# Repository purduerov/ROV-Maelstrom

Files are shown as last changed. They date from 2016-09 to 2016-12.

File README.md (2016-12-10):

# ROV-Maelstrom

Purdue IEEE designed an ROV (Remotely Operated underwater Vehicle) to compete in the 2016 [MATE international competition](http://www.marinetech.org/rov-competition-2/). ROV *Maelstrom* was the cumulation of this effort that resulted in a 13th place finish. For more information visit [purdueieee.org/rov](http://purdueieee.org/rov).

Our design is hearby open-sourced in order to share what we have done with other MATE teams and those who are interested. While not all of our designs worked as planned, we share these files in order to assist thoughs who may need it and inspire others with these ideas.

Maelstrom

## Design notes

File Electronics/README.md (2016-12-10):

# ROV-Maelstrom-Electronics

ROV Maelstrom’s electronics were designed to facilitate easy and reliable command over the course of the ROV’s lifetime. Command starts at the Control Center, the surface electronics that the user interfaces with. This includes a laptop computer, a network router, and a 48 V power supply protected with a 40-A fuse. 

Communication with the Control Center is done through the tether with a Category 5 Ethernet cable, which provides high bandwidth and noise immunity. The power is transmitted through two 12-AWG marine wires. Onboard the ROV, it steps down the 48 V to 12 V, 5 V, and 3.3 V for use by the ROV’s eight T200 thrusters, the hydraulics motor, and the Main Electronics inside the Electronics Tube. The Power Distribution Box contains the Power Distribution Board, which handles the 48 V to 12 V power conversion and thruster control. Inside of the Electronics Tube are the Main Microcontroller Board, the Power Regulator Board, and the Application Board which are all connected via the Backplane. The Main Microcontroller Board handles the central logic processing of the ROV and communication with the surface, Application Board, and Power Distribution Board. The Power Regulator Board supplies the 5 V required by the electronics inside of the Electronics Tube, while the Application Board controls the LED lighting of ROV Maelstrom. The Navigation Board is used for pressure and attitude measurements and is placed outside of the Electronics Tube for reduced magnetic interference and direct contact with water. The board also hosts the sonar transmitter used for GPS-like navigation. The Sonar Receiver Board in the Control Center is used to receive and filter the sonar transmission signals. The printed circuit boards were designed in-house with the use of CadSoft's EAGLE software and then hand populated

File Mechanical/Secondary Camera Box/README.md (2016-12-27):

# Secondary Camera Boxes

These are the boxes for the secondary cameras. They are not able to rotate like the primary camera tube.

The cameras themselves had a  1-2 second delay since they were cheaper than the main camera and webcams couldn't easily be used with the STM32F4 microcontroller.

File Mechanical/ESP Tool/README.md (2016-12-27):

# ESP Tool

The Environmental Sample Processor(ESP) tool was designed to pick up the ESP cable connector and attach it to the power and communications hub in the water. The part was not fully manufactured or tested.

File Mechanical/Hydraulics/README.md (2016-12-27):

# Hydraulics

The hydraulic system had an open loop design, and pulled in pool water, pressurized it, and sent it to a solenoid. The water was distributed by the solenoid and used to actuate the main claw, ESP tool, Wellhead tool, and other manipulators. After being used, it returned to the pool water. We used an M100 waterproof motor to power the pump. The solenoid was in an open faced housing, and filled with Magic Gel, a potting substance that sets to the consistency of gelatin. The Magic Gel insulated and water proofed the solenoid. While effective, it is permanent and needs to be removed before working on it and reapplied. We used a hydraulic system instead of electric motors for direct actuation to make waterproofing the system easier. Due to electrical issues the full system was never operated on the vehicle.

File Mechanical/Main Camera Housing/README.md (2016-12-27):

# Main Camera Housing 

The Camera housing is made from a polycarbonate tube and two aluminum endcaps. The camera is mounted onto a servo in the middle of the tube, and the servo is attached by a dowel to the endcap. This allows the camera to spin and gives the pilot a 180 degree field a view. The endcaps are sealed with two x-profile o-rings. 

For the cameras themselves we used IP addressable cameras for ROV Maelstrom. The signals from these cameras were then passed to an Ethernet switch. This switch then handled figuring out what information needed to be sent to the surface.

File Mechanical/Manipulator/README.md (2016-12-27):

# Manipulator

The manipulator is driven from a hydraulic piston attached to a base. There are three fingers attached to the base, with two on the top and one on the bottom. The design is optimized to pick up pipes, the most common prop in the competition.  The tips on the claw are 3D printed, allowing for several designs to be made, and quick changes between the two tips.

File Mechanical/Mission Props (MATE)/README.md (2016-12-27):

# Mission Props

These are the props provided to the team by the MATE competition.

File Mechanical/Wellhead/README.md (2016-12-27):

# Wellhead

The wellhead tool has four grooves in it to position bolts so that they can be installed in one attempt. It requires that a person positions the bolts in the tool by hand. The tool will then clamp down on them. The ROV then moves over the wellhead and aligns the bolts. When the tool releases the bolts, then all drop into place in their correct positions.

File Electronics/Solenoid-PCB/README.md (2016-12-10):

# Solenoid-PCB
This board contains a shift register to control solenoids on the ROV.

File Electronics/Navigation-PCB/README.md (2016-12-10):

# ROV-Maelstrom-Navboard

This board contains the IMU to assist with ROV positioning. Additionally it containspiezo driver to send pulses to the sonar receiver board. The full sonar system was never fullly implemented this season.

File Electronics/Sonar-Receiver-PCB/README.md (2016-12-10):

# PCB-Maelstrom-Sonar-Receiver

The sonar receiver board is placed at the surface of the pool. It receives the piezo pulses from the ROV and uses the information to pinpoint the ROV's position underwater. The full sonar system was never fullly implemented this season.

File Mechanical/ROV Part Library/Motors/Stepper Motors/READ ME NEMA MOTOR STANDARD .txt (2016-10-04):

NEMA Motor Standard

There is no NEMA motor naming convention due to the fact that all NEMA Motor Sizes 
are controlled with Configurations.  Therefore there is absolutely no need to add 
any new files to this folder.

If you need a NEMA Stepper Motor Size and you do not know what a configuration is or 
how to use them, please contact the Mechanical Team Lead 
(Joshua Berg -> berg30@purdue.edu)

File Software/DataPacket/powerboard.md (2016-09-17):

# PowerBoard CAN Communication

Main Micro -> PowerBoard Micro (Packet 1)
-----------------------------------------
Byte # |   Description   | Type
-------|-----------------|------
  00   |   Packet Type   |  0x48 - 'H'
  01   |        T1       |	Signed int (1 byte)
  02   |        T2       |  Signed int (1 byte)
  03   |        T3       |	Signed int (1 byte)
  04   |        T4       |  Signed int (1 byte)
  05   |       Empty     |	Empty
  06   |       Empty     |  Empty
  07   |     Pump ESC    |  1 byte (0 to 255 PWM Val)
  
Main Micro -> PowerBoard Micro (Packet 2)
-----------------------------------------
Byte # |   Description   | Type
-------|-----------------|------
  00   |   Packet Type   |  0x56 - 'V'
  01   |        T5       |	Signed int (1 byte)
  02   |        T6       |  Signed int (1 byte)
  03   |        T7       |	Signed int (1 byte)
  04   |        T8       |  Signed int (1 byte)
  05   |       Empty     |	Empty
  06   |       Empty     |  Empty
  07   |       Empty     |  1 byte - bool for pid / manual control

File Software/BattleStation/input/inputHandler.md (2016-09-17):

initInputHandler()
	init SDL library
	while the program is running
		check if there's a new joystick
		if so
			update queue of joysticks
			assign button-to-function mapping
			show it on GUI
		check if there's a missing joystick
		if so
			update queue
			show it on GUI
		check if button from any joysticks were pressed
		if so
			call function

a vector of SDL_Joystick* will be used to hold joysticks

Questions
1. How do I know that a joystick is unplugged?
2. If someone unplugs and replugs really quickly, will it slow the button input from my program? And if so, how much?
3. If someone unpluags and replugs a new joystick, in between the two checks, how do I know if they are different joysticks? (will they have the same ID?)
4. how do I show it on GUI?
5.

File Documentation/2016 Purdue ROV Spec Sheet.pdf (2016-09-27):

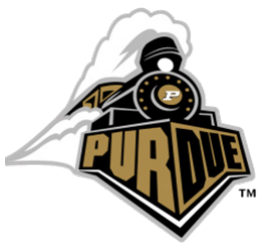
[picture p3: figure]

# PROVEN ROBOTICS

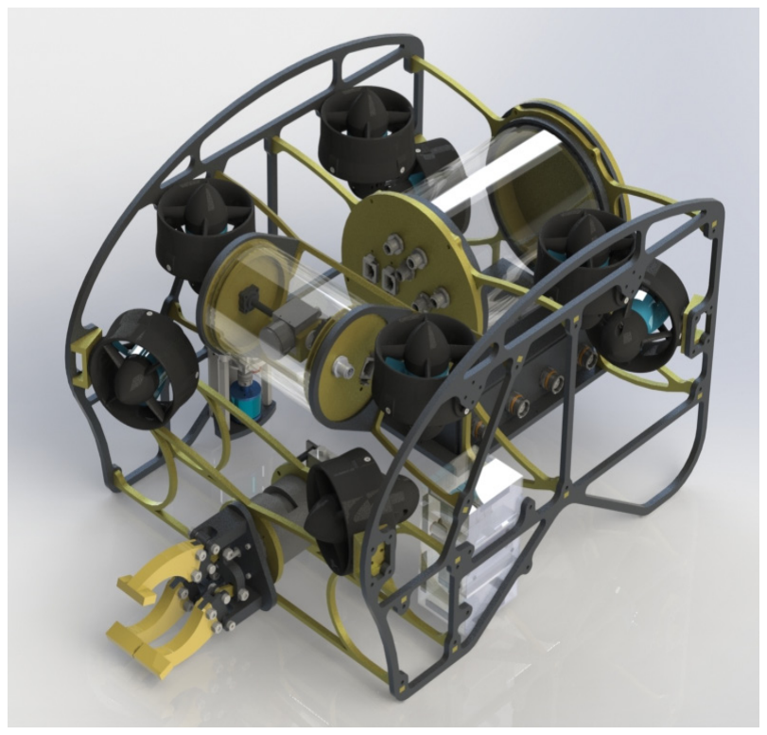
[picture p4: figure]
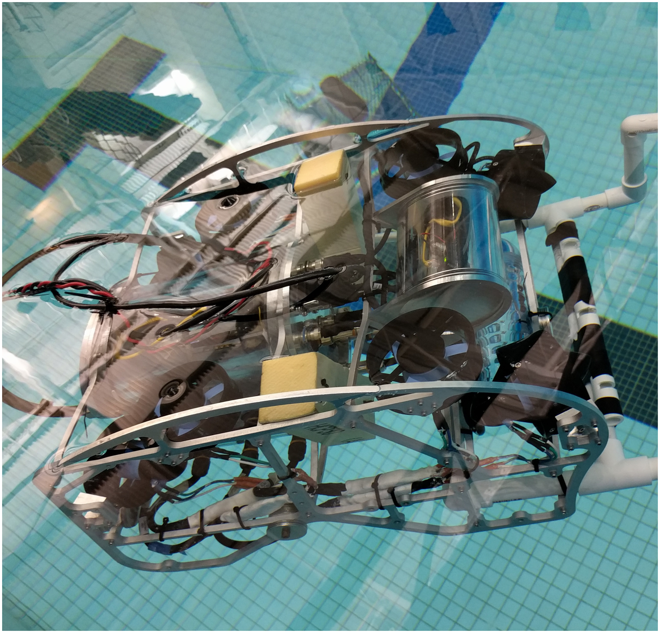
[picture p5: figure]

# ROV MAELSTROM

### West Lafayette, Indiana, USA

Total Mass in Air:
12.8 kg

Overall Dimensions:
48.3 cm x 39.4 cm x 33.0 cm

Primary Material:
Aluminum 6061 T-6
Stainless Steel
Polycarbonate

Total Cost of ROV:
$10,500

Total ROV Design Man-Hours: 6,500 hours

Safety Features:
Enclosed Pump
Fused Main Power
Shrouded Propellers
Software Disconnection Timeouts Hydraulics Pressure Release Valve Epoxy and Heat Shrink Sealed Wires

Special Features:
Onboard Open-Loop Hydraulics LED-Illuminated Camera with Tilt Custom Built On-Board Electronic System Four-Axis Sonar Based Positioning System

Carolyn Leweling

Electrical Engineering
Sophomore: Lead Sponsorship Coordinator
Electrical Team
2nd Year Competing

Dan Schillizzi

Mechanical Engineering
Sophomore: Mechanical Team 2nd Year Competing

Joseph Pejril

Mechanical Engineering
Junior: Mechanical Team
ROV Pilot
2nd Year Competing

Kyle Rakos

Computer Engineering
Junior: CEO
2nd Year Competing

Luke McBee

Computer Engineering
Sophomore: Electrical
Team Lead
2nd Year Competing

Matt Molo

Computer Science
Junior: Software Team Lead ROV Pilot
3rd Year Competing

Rodolfo E. Leiva

Electrical Engineering
Junior: Electrical Team
2nd Year Competing

Ryan McBee

Computer Engineering
Sophomore: Embedded
Software Subteam Lead
2nd Year Competing

Samuel Deghuee

Electrical Engineering
Sophomore: Electrical Team 2nd Year Competing

Sanay Shah

Industrial Engineering
Sophomore: COO
2nd Year Competing

Teal Dowd

Mechanical Engineering
Sophomore: Mechanical Team 2nd Year Competing

Joshua Berg

Mechanical Engineering
Junior: Mechanical Team Lead 2nd Year Competing

Charlie Su

Computer Science/Physics
Sophomore: Software Team
2nd Year Competing

Alex Ruffino

Mechanical Engineering
Freshman: Sponsorship
Coordinator
Mechanical Team
1st Year Competing

Rohit Srivastava

Biomedical Engineering
Freshman: Mechanical Team
1st Year Competing

Ajay Gopakumar

Computer Engineering
Freshman: Software Team
1st Year Competing

Nicholas Loffredo

Electrical Engineering
Sophomore: Electrical Team 1st Year Competing

Henry Shi

Industrial Engineering
Sophomore: Technical Writer 1st Year Competing

Yuqin (Sophia) Duan

Computer Engineering
Freshman: Software &
Mechanical Team
1st Year Competing

Jared Borg

Mechanical Engineering
Freshman: Mechanical Team
5th Year Competing

Scott Giammatteo

Aerospace Engineering
Freshman: Mechanical Team
1st Year Competing

Mimansa Verma

Computer Engineering
Freshman: Software Team
1st Year Competing

Jakob Andrén

Engineering Physics
Senior: Electrical &
Software Team
1st Year Competing

Michael Reeves

Physics/Computer Science
Freshman: Software Team
1st Year Competing

Nathan Glotzbach

Physics
Freshman: Software Team
1st Year Competing

Ben Maxfield

Computer Science
Freshman: Software Team
1st Year Competing

Oksana Makarova

Electrical Engineering/Physics Freshman: Software Team
1st Year Competing

Katie Lothrop

Mechanical Engineering
Sophomore: Mechanical Team 1st Year Competing

Amandeep Singh

Mechanical Engineering
Sophomore: Software Team
1st Year Competing

McKenzie White

Environmental and Ecological Engineering
Freshman: Mechanical Team
1st Year Competing

Joel Copi

Computer Engineering
Freshman: Software Team
1st Year Competing

Bayley Clausen

Mechanical Engineering
Junior: Electrical Team
2nd Year Competing

Jason King

Computer Engineering
Freshman: Software Team
1st Year Competing

Alan Han

Electrical Engineering
Sophomore: Electrical Team 1st Year Competing

2015 Finish: 15th Place
Estimated Travel: 1,1418 km Year Competing: Seventh Year Members: College Freshman - Senior

Xinyi Jiang

Electrical Engineering
Sophomore Electrical Team
1st Year Competing

Brandon Stewart

Computer Science
Freshman: Software Team
1st Year Competing

Alex Gebhardt

Mechanical Engineering
Freshman: Mechanical Team
1st Year Competing

John Lee

Computer Engineering
Senior: ROV Pilot
1st Year Competing

Ashiq Kurian

Industrial Engineering
Sophomore: Poster Designer 1st Year Competing

Charles Li

Electrical Engineering
Sophomore: Electrical Team 1st Year Competing

## Purdue University IEEE ROV Team

Administrative Team

Software Team
Matthew Molo
Ryan McBee
Yuqin Duan
Jason King
Joel Copi
Vyaas Shankar
Oksana Makarova
Ajay Gopakumar

Mikey Reeves
Nathan Glotzbach
Brandon Stewart
Adam Kranz
Ben Maxfield
Charlie Su
Mimansa Verma
Jakob Andren

Electrical Team
Luke McBee
Rodolfo Leiva
Wen Shen Mow
Austin White
Dimcho Karakashev
Jakob Andren
Jeff Geiss
Alan Han
Qiyue Liang
Paul Swartz
Charles Li
Carolyn Lewelling
Bayley Clausen
Xinyi Jiang
Nicholas Loffredo

Mechanical Team
Joshua Berg
Amandeep Singh
Tom Lorenc
Teal Dowd
Dan Schillizzi
Alex Ruffino
Rohit Srivastava
Jared Borg
McKenzie White
Joseph Pejril
Yuqin Duan
Scott Giammatteo
Katie Lothrop

Kyle Rakos
Sanay Shah
Luke McBee
Joshua Berg
Matthew Molo
Ryan Mcbee
Carolyn Lewelling
Alex Ruffino
Ashiq Kurian
Henry Shi

CEO
COO
Electrical Team Lead
Mechanical Team Lead
Software Team Lead & ROV Pilot Embedded Software Subteam Lead Lead Sponsorship Coordinator Sponsorship Coordinator
Poster Designer
Technical Writer

Pilots
Matthew Molo
Jospeh Pejril
John Lee

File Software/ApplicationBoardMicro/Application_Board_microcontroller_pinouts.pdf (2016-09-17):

## Applicaton-Board Project Configuration Report

# 1. Description

## 1.1. Project

Project Name | Applicaton-Board
Board Name | Applicaton-Board
Generated with: | STM32CubeMX 4.11.0
Date | 12/02/2015

## 1.2. MCU

MCU Series | STM32F4
MCU Line | STM32F405/415
MCU name | STM32F405RGTx
MCU Package | LQFP64
MCU Pin number | 64

# 2. Pinout Configuration

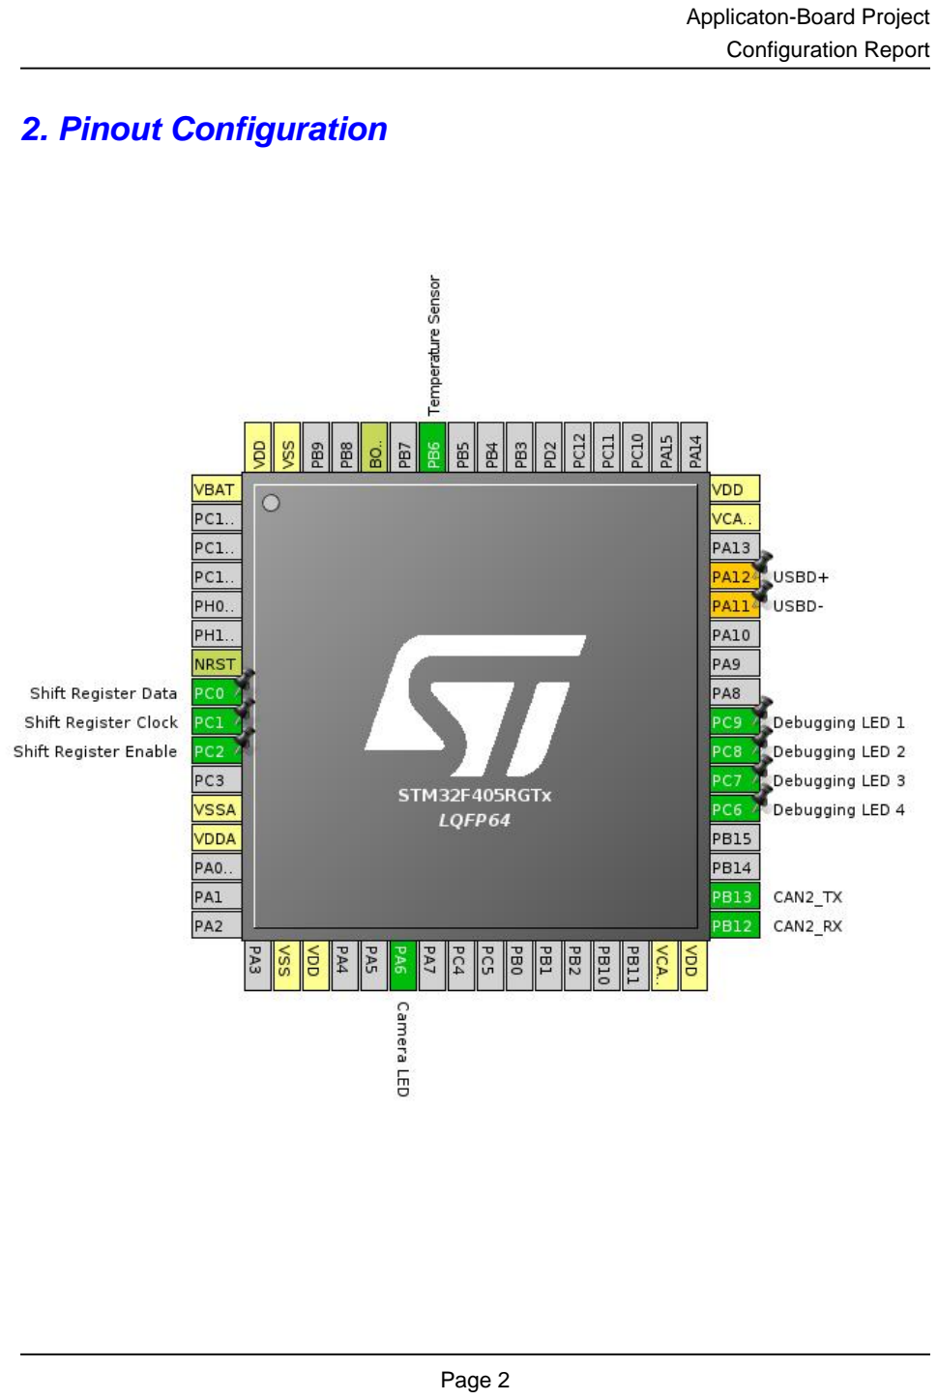
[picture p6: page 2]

# 3. Pins Configuration

Pin Number LQFP64 | Pin Name (function after reset) | Pin Type | Alternate Function(s) | Label
1 | VBAT | Power
7 | NRST | Reset
8 | PC0 * | I/O | GPIO_Output | Shift Register Data
9 | PC1 * | I/O | GPIO_Input | Shift Register Clock
10 | PC2 * | I/O | GPIO_Output | Shift Register Enable
12 | VSSA | Power
13 | VDDA | Power
18 | VSS | Power
19 | VDD | Power
22 | PA6 | I/O | TIM3_CH1 | Camera LED
31 | VCAP_1 | Power
32 | VDD | Power
33 | PB12 | I/O | CAN2_RX
34 | PB13 | I/O | CAN2_TX
37 | PC6 * | I/O | GPIO_Output | Debugging LED 4
38 | PC7 * | I/O | GPIO_Output | Debugging LED 3
39 | PC8 * | I/O | GPIO_Output | Debugging LED 2
40 | PC9 * | I/O | GPIO_Output | Debugging LED 1
44 | PA11 ** | I/O | USB_OTG_FS_DM | USBD-
45 | PA12 ** | I/O | USB_OTG_FS_DP | USBD+
47 | VCAP_2 | Power
48 | VDD | Power
58 | PB6 | I/O | TIM4_CH1 | Temperature Sensor
60 | BOOT0 | Boot
63 | VSS | Power
64 | VDD | Power

## * The pin is affected with an I/O function ** The pin is affected with a peripheral function but no peripheral mode is activated

# 4. Clock Tree Configuration

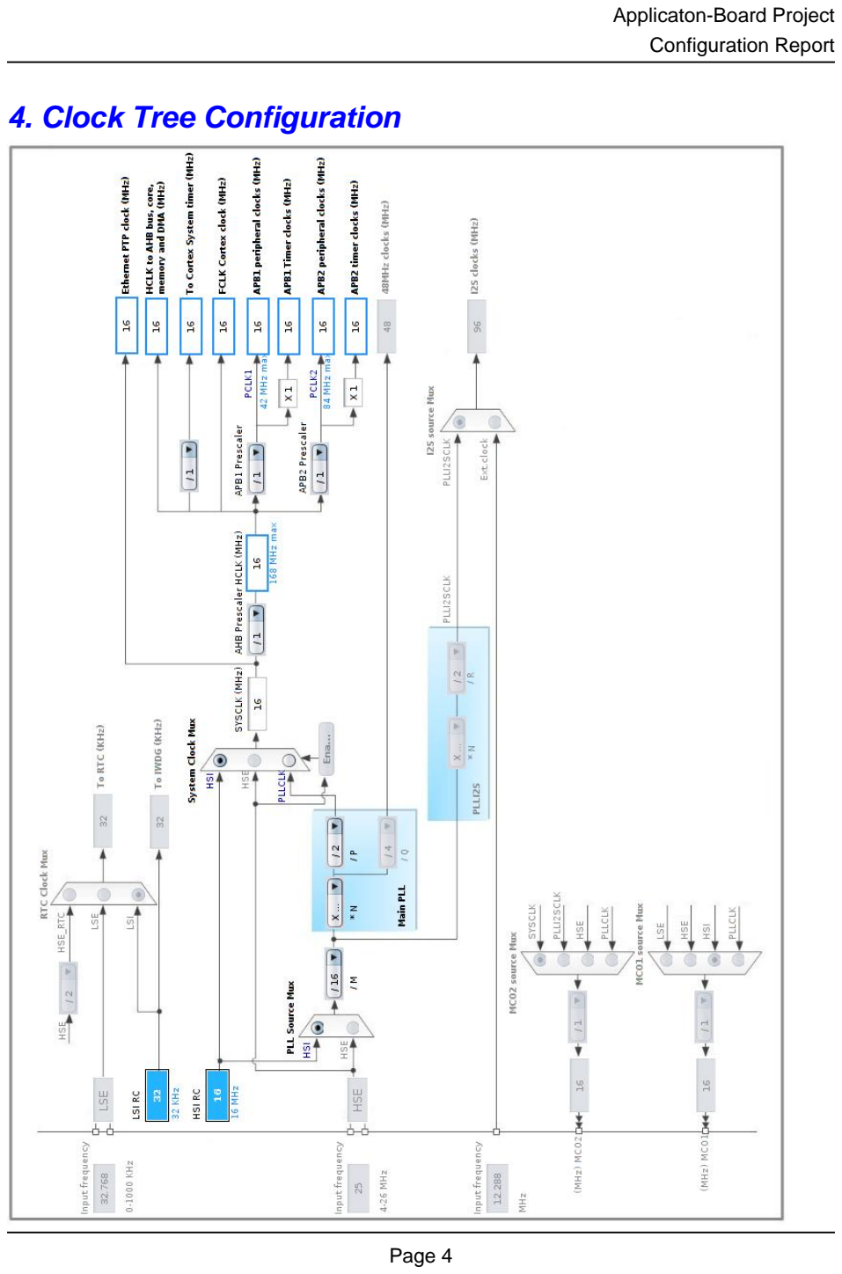
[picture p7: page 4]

# 5. IPs and Middleware Configuration

# 5.1. CAN2

## mode: Mode

## 5.1.1. Parameter Settings:

### Bit Timings Parameters:

Prescaler (for Time Quantum) | 16
Time Quantum | 1000.0 *
Time Quanta in Bit Segment 1 | 1 Time
Time Quanta in Bit Segment 2 | 1 Time
Time for one Bit | 3000 *
ReSynchronization Jump Width | 1 Time

### Basic Parameters:

Time Triggered Communication Mode | Disable
Automatic Bus-Off Management | Disable
Automatic Wake-Up Mode | Disable
No-Automatic Retransmission | Disable
Receive Fifo Locked Mode | Disable
Transmit Fifo Priority | Disable

### Advanced Parameters:

Operating Mode | Normal

# 5.2. TIM3

## Channel1: PWM Generation CH1

## 5.2.1. Parameter Settings:

### Counter Settings:

Prescaler (PSC - 16 bits value) | 0
Counter Mode | Up
Counter Period (AutoReload Register - 16 bits value ) | 0
Internal Clock Division (CKD) | No Division

### Trigger Output (TRGO) Parameters:

Master/Slave Mode | Disable (no sync between this TIM (Master) and its Slaves

Trigger Event Selection | Reset (UG bit from TIMx_EGR)

### PWM Generation Channel 1:

Mode | PWM mode 1
Pulse (16 bits value) | 0
Fast Mode | Disable
CH Polarity | High

# 5.3. TIM4

## Channel1: PWM Generation CH1

## 5.3.1. Parameter Settings:

### Counter Settings:

Prescaler (PSC - 16 bits value) | 0
Counter Mode | Up
Counter Period (AutoReload Register - 16 bits value ) | 0
Internal Clock Division (CKD) | No Division

### Trigger Output (TRGO) Parameters:

Master/Slave Mode | Disable (no sync between this TIM (Master) and its Slaves
Trigger Event Selection | Reset (UG bit from TIMx_EGR)

### PWM Generation Channel 1:

Mode | PWM mode 1
Pulse (16 bits value) | 0
Fast Mode | Disable
CH Polarity | High

### * User modified value

# 6. System Configuration

# 6.1. GPIO configuration

IP | Pin | Signal | GPIO mode | GPIO pull/up pull down | Max Speed | User Label
CAN2 | PB12 | CAN2_RX | Alternate Function Push Pull | No pull-up and no pull-down | High *
| PB13 | CAN2_TX | Alternate Function Push Pull | No pull-up and no pull-down | High *
TIM3 | PA6 | TIM3_CH1 | Alternate Function Push Pull | No pull-up and no pull-down | Low | Camera LED
TIM4 | PB6 | TIM4_CH1 | Alternate Function Push Pull | No pull-up and no pull-down | Low | Temperature Sensor
Single Mapped Signals | PA11 | USB_OTG_FS_ DM | Alternate Function Push Pull | No pull-up and no pull-down | High * | USBD-
| PA12 | USB_OTG_FS_ DP | Alternate Function Push Pull | No pull-up and no pull-down | High * | USBD+
GPIO | PC0 | GPIO_Output | Output Push Pull | No pull-up and no pull-down | Low | Shift Register Data
| PC1 | GPIO_Input | Input mode | No pull-up and no pull-down | n/a | Shift Register Clock
| PC2 | GPIO_Output | Output Push Pull | No pull-up and no pull-down | Low | Shift Register Enable
| PC6 | GPIO_Output | Output Push Pull | No pull-up and no pull-down | Low | Debugging LED 4
| PC7 | GPIO_Output | Output Push Pull | No pull-up and no pull-down | Low | Debugging LED 3
| PC8 | GPIO_Output | Output Push Pull | No pull-up and no pull-down | Low | Debugging LED 2
| PC9 | GPIO_Output | Output Push Pull | No pull-up and no pull-down | Low | Debugging LED 1

# 6.2. DMA configuration

## nothing configured in DMA service

# 6.3. NVIC configuration

Interrupt Table | Enable | Preenmption Priority | SubPriority
System tick timer | true | 0 | 0
Non maskable interrupt | unused
Memory management fault | unused
Pre-fetch fault, memory access fault | unused
Undefined instruction or illegal state | unused
Debug monitor | unused
PVD interrupt through EXTI line 16 | unused
Flash global interrupt | unused
RCC global interrupt | unused
TIM3 global interrupt | unused
TIM4 global interrupt | unused
CAN2 TX interrupts | unused
CAN2 RX0 interrupts | unused
CAN2 RX1 interrupt | unused
CAN2 SCE interrupt | unused

### * User modified value

# 7. Power Plugin report

## 7.1. Microcontroller Selection

Series | STM32F4
Line | STM32F405/415
MCU | STM32F405RGTx
Datasheet | 022152_Rev5

## 7.2. Parameter Selection

Temperature | 25
Vdd | 3.3

# 8. Software Project

## 8.1. Project Settings

Name | Value
Project Name | Applicaton-Board
Project Folder | /home/lukeinator/Documents/Applicaton-Board
Toolchain / IDE | EWARM
Firmware Package Name and Version | STM32Cube FW_F4 V1.9.0

## 8.2. Code Generation Settings

Name | Value
STM32Cube Firmware Library Package | Copy all used libraries into the project folder
Generate peripheral initialization as a pair of '.c/.h' files | No
Backup previously generated files when re-generating | No
Delete previously generated files when not re-generated | Yes
Set all free pins as analog (to optimize the power consumption) | No

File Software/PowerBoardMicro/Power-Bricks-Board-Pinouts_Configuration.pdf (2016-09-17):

## Power-Bricks-Board-Pinouts Project Configuration Report

# 1. Description

## 1.1. Project

Project Name | Power-Bricks-Board-Pinouts
Board Name | Power-Bricks-Board-Pinouts
Generated with: | STM32CubeMX 4.11.0
Date | 12/10/2015

## 1.2. MCU

MCU Series | STM32F4
MCU Line | STM32F405/415
MCU name | STM32F405RGTx
MCU Package | LQFP64
MCU Pin number | 64

# 2. Pinout Configuration

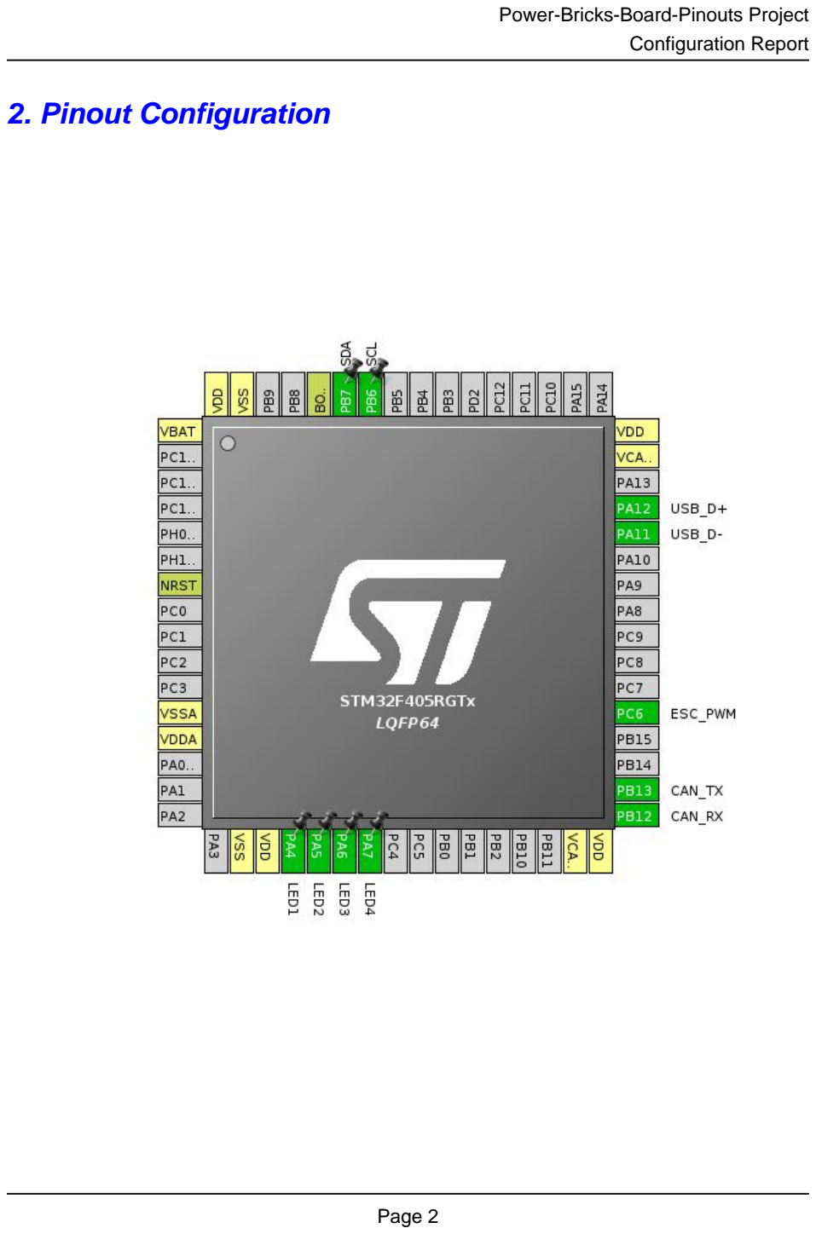
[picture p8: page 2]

# 3. Pins Configuration

Pin Number LQFP64 | Pin Name (function after reset) | Pin Type | Alternate Function(s) | Label
1 | VBAT | Power
7 | NRST | Reset
12 | VSSA | Power
13 | VDDA | Power
18 | VSS | Power
19 | VDD | Power
20 | PA4 * | I/O | GPIO_Output | LED1
21 | PA5 * | I/O | GPIO_Output | LED2
22 | PA6 * | I/O | GPIO_Output | LED3
23 | PA7 * | I/O | GPIO_Output | LED4
31 | VCAP_1 | Power
32 | VDD | Power
33 | PB12 | I/O | CAN2_RX | CAN_RX
34 | PB13 | I/O | CAN2_TX | CAN_TX
37 | PC6 | I/O | TIM3_CH1 | ESC_PWM
44 | PA11 | I/O | USB_OTG_FS_DM | USB_D-
45 | PA12 | I/O | USB_OTG_FS_DP | USB_D+
47 | VCAP_2 | Power
48 | VDD | Power
58 | PB6 | I/O | I2C1_SCL | SCL
59 | PB7 | I/O | I2C1_SDA | SDA
60 | BOOT0 | Boot
63 | VSS | Power
64 | VDD | Power

## * The pin is affected with an I/O function

# 4. Clock Tree Configuration

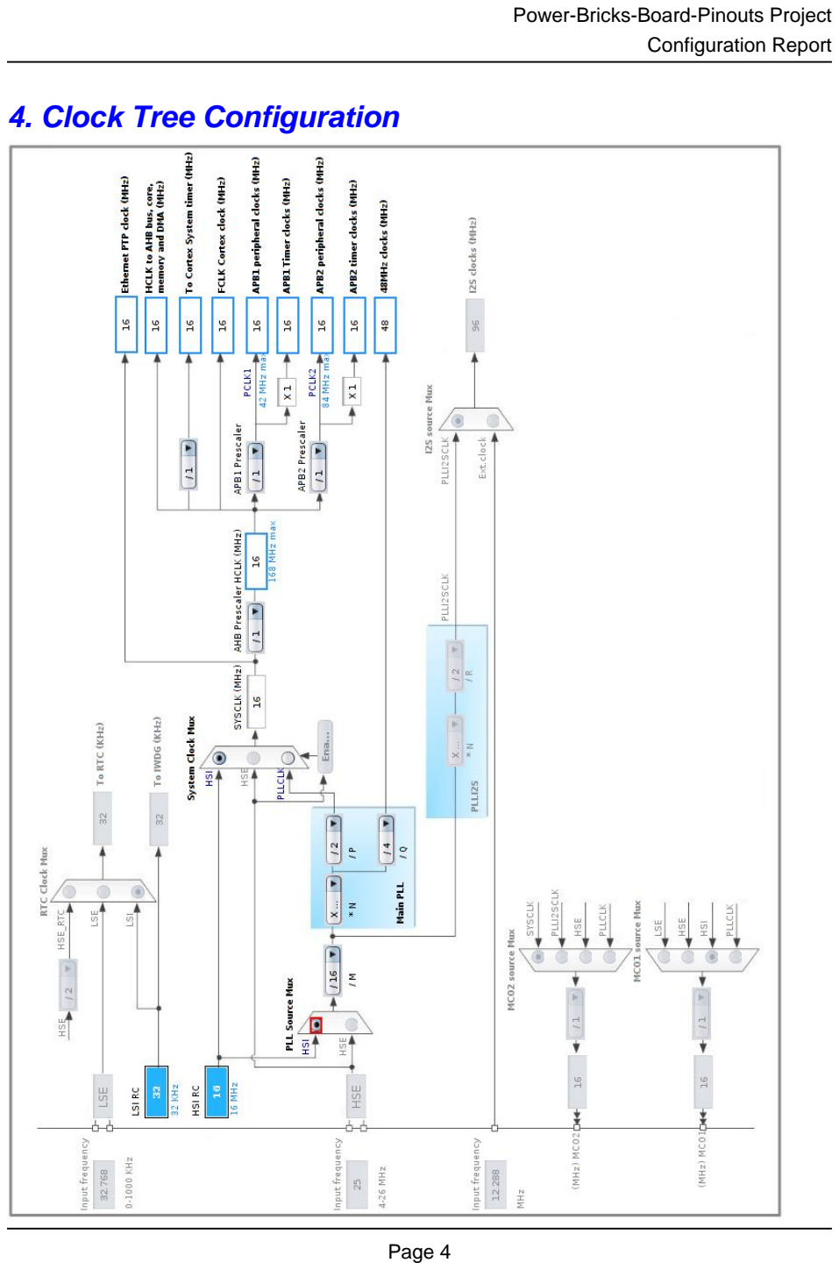
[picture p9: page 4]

# 5. IPs and Middleware Configuration

# 5.1. CAN2

## mode: Mode

## 5.1.1. Parameter Settings:

### Bit Timings Parameters:

Prescaler (for Time Quantum) | 16
Time Quantum | 1000.0 *
Time Quanta in Bit Segment 1 | 1 Time
Time Quanta in Bit Segment 2 | 1 Time
Time for one Bit | 3000 *
ReSynchronization Jump Width | 1 Time

### Basic Parameters:

Time Triggered Communication Mode | Disable
Automatic Bus-Off Management | Disable
Automatic Wake-Up Mode | Disable
No-Automatic Retransmission | Disable
Receive Fifo Locked Mode | Disable
Transmit Fifo Priority | Disable

### Advanced Parameters:

Operating Mode | Normal

# 5.2. I2C1

## I2C: I2C

## 5.2.1. Parameter Settings:

### Master Features:

I2C Speed Mode | Standard Mode
I2C Clock Speed (Hz) | 100000

### Slave Features:

Clock No Stretch Mode | Disabled
Primary Address Length selection | 7-bit
Dual Address Acknowledged | Disabled

Primary slave address | 0
General Call address detection | Disabled

# 5.3. TIM3

## Channel1: PWM Generation CH1

## 5.3.1. Parameter Settings:

### Counter Settings:

Prescaler (PSC - 16 bits value) | 0
Counter Mode | Up
Counter Period (AutoReload Register - 16 bits value ) | 0
Internal Clock Division (CKD) | No Division

### Trigger Output (TRGO) Parameters:

Master/Slave Mode | Disable (no sync between this TIM (Master) and its Slaves
Trigger Event Selection | Reset (UG bit from TIMx_EGR)

### PWM Generation Channel 1:

Mode | PWM mode 1
Pulse (16 bits value) | 0
Fast Mode | Disable
CH Polarity | High

# 5.4. USB_OTG_FS

## Mode: Device_Only

## 5.4.1. Parameter Settings:

Speed | Device Full Speed 12MBit/s
Endpoint 0 Max Packet size | 64 Bytes
Enable internal IP DMA | Disabled
Low power | Disabled
Link Power Management | Disabled
VBUS sensing | Enabled

### * User modified value

# 6. System Configuration

# 6.1. GPIO configuration

IP | Pin | Signal | GPIO mode | GPIO pull/up pull down | Max Speed | User Label
CAN2 | PB12 | CAN2_RX | Alternate Function Push Pull | No pull-up and no pull-down | High * | CAN_RX
| PB13 | CAN2_TX | Alternate Function Push Pull | No pull-up and no pull-down | High * | CAN_TX
I2C1 | PB6 | I2C1_SCL | Alternate Function Open Drain | Pull-up | High * | SCL
| PB7 | I2C1_SDA | Alternate Function Open Drain | Pull-up | High * | SDA
TIM3 | PC6 | TIM3_CH1 | Alternate Function Push Pull | No pull-up and no pull-down | Low | ESC_PWM
USB_OTG_ FS | PA11 | USB_OTG_FS_ DM | Alternate Function Push Pull | No pull-up and no pull-down | High * | USB_D-
| PA12 | USB_OTG_FS_ DP | Alternate Function Push Pull | No pull-up and no pull-down | High * | USB_D+
GPIO | PA4 | GPIO_Output | Output Push Pull | No pull-up and no pull-down | Low | LED1
| PA5 | GPIO_Output | Output Push Pull | No pull-up and no pull-down | Low | LED2
| PA6 | GPIO_Output | Output Push Pull | No pull-up and no pull-down | Low | LED3
| PA7 | GPIO_Output | Output Push Pull | No pull-up and no pull-down | Low | LED4

# 6.2. DMA configuration

## nothing configured in DMA service

# 6.3. NVIC configuration

Interrupt Table | Enable | Preenmption Priority | SubPriority
System tick timer | true | 0 | 0
Non maskable interrupt | unused
Memory management fault | unused
Pre-fetch fault, memory access fault | unused
Undefined instruction or illegal state | unused
Debug monitor | unused
PVD interrupt through EXTI line 16 | unused
Flash global interrupt | unused
RCC global interrupt | unused
TIM3 global interrupt | unused
I2C1 event interrupt | unused
I2C1 error interrupt | unused
CAN2 TX interrupts | unused
CAN2 RX0 interrupts | unused
CAN2 RX1 interrupt | unused
CAN2 SCE interrupt | unused
USB On The Go FS global interrupt | unused

### * User modified value

# 7. Power Plugin report

## 7.1. Microcontroller Selection

Series | STM32F4
Line | STM32F405/415
MCU | STM32F405RGTx
Datasheet | 022152_Rev5

## 7.2. Parameter Selection

Temperature | 25
Vdd | 3.3

# 8. Software Project

## 8.1. Project Settings

Name | Value
Project Name | Power-Bricks-Board-Pinouts
Project Folder | /home/lukeinator/Documents/Power-Bricks-Board-Pinouts
Toolchain / IDE | EWARM
Firmware Package Name and Version | STM32Cube FW_F4 V1.9.0

## 8.2. Code Generation Settings

Name | Value
STM32Cube Firmware Library Package | Copy all used libraries into the project folder
Generate peripheral initialization as a pair of '.c/.h' files | No
Backup previously generated files when re-generating | No
Delete previously generated files when not re-generated | Yes
Set all free pins as analog (to optimize the power consumption) | No

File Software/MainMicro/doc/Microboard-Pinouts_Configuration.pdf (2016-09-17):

## Microboard-Pinouts Project Configuration Report

# 1. Description

## 1.1. Project

Project Name | Microboard-Pinouts
Board Name | Microboard-Pinouts
Generated with: | STM32CubeMX 4.11.0
Date | 12/03/2015

## 1.2. MCU

MCU Series | STM32F4
MCU Line | STM32F407/417
MCU name | STM32F407VGTx
MCU Package | LQFP100
MCU Pin number | 100

# 2. Pinout Configuration

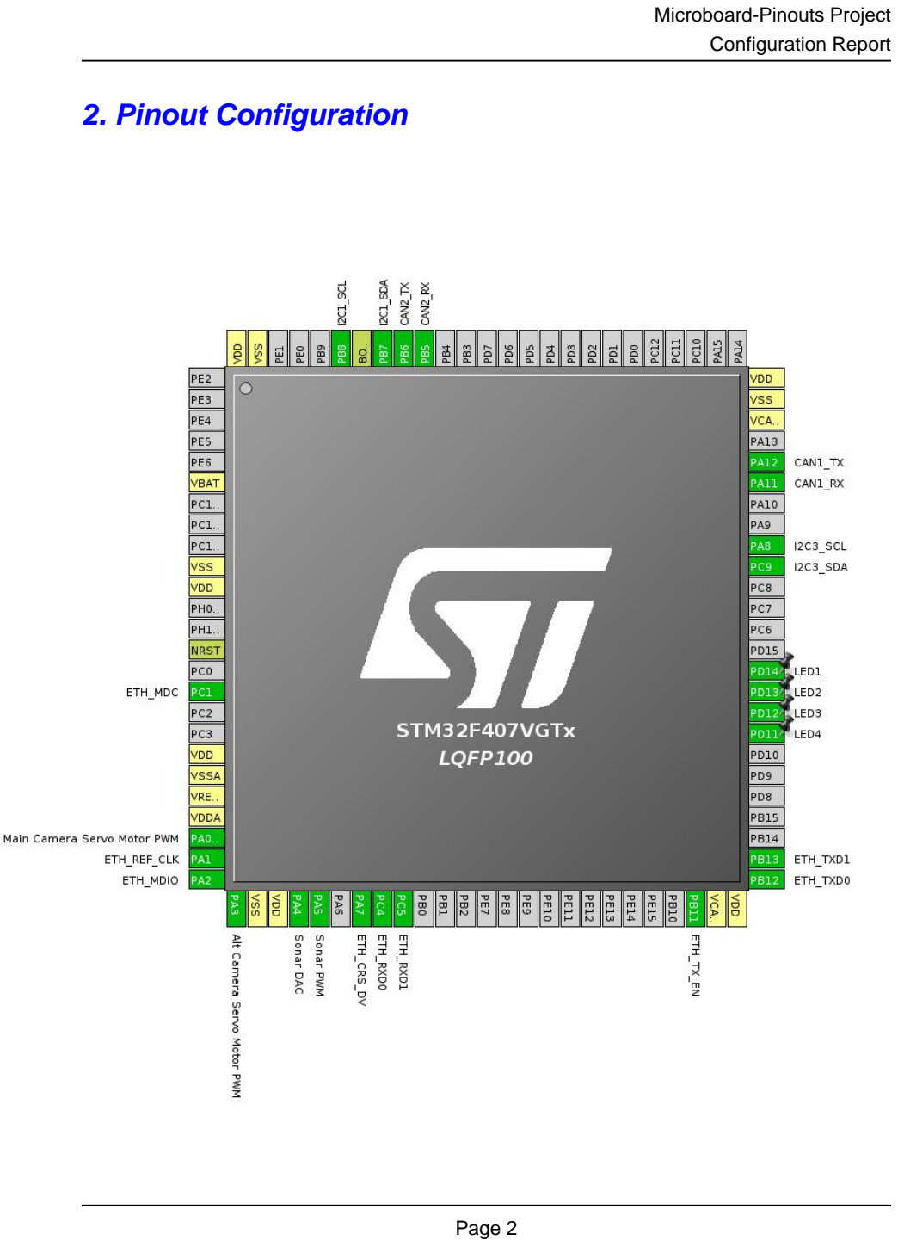
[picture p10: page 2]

# 3. Pins Configuration

Pin Number LQFP100 | Pin Name (function after reset) | Pin Type | Alternate Function(s) | Label
6 | VBAT | Power
10 | VSS | Power
11 | VDD | Power
14 | NRST | Reset
16 | PC1 | I/O | ETH_MDC
19 | VDD | Power
20 | VSSA | Power
21 | VREF+ | Power
22 | VDDA | Power
23 | PA0-WKUP | I/O | TIM5_CH1 | Main Camera Servo Motor PWM
24 | PA1 | I/O | ETH_REF_CLK
25 | PA2 | I/O | ETH_MDIO
26 | PA3 | I/O | TIM5_CH4 | Alt Camera Servo Motor PWM
27 | VSS | Power
28 | VDD | Power
29 | PA4 | I/O | DAC_OUT1 | Sonar DAC
30 | PA5 | I/O | TIM2_CH1 | Sonar PWM
32 | PA7 | I/O | ETH_CRS_DV
33 | PC4 | I/O | ETH_RXD0
34 | PC5 | I/O | ETH_RXD1
48 | PB11 | I/O | ETH_TX_EN
49 | VCAP_1 | Power
50 | VDD | Power
51 | PB12 | I/O | ETH_TXD0
52 | PB13 | I/O | ETH_TXD1
58 | PD11 * | I/O | GPIO_Output | LED4
59 | PD12 * | I/O | GPIO_Output | LED3
60 | PD13 * | I/O | GPIO_Input | LED2
61 | PD14 * | I/O | GPIO_Output | LED1
66 | PC9 | I/O | I2C3_SDA
67 | PA8 | I/O | I2C3_SCL
70 | PA11 | I/O | CAN1_RX
71 | PA12 | I/O | CAN1_TX
73 | VCAP_2 | Power

Pin Number LQFP100 | Pin Name (function after reset) | Pin Type | Alternate Function(s) | Label
74 | VSS | Power
75 | VDD | Power
91 | PB5 | I/O | CAN2_RX
92 | PB6 | I/O | CAN2_TX
93 | PB7 | I/O | I2C1_SDA
94 | BOOT0 | Boot
95 | PB8 | I/O | I2C1_SCL
99 | VSS | Power
100 | VDD | Power

## * The pin is affected with an I/O function

# 4. Clock Tree Configuration

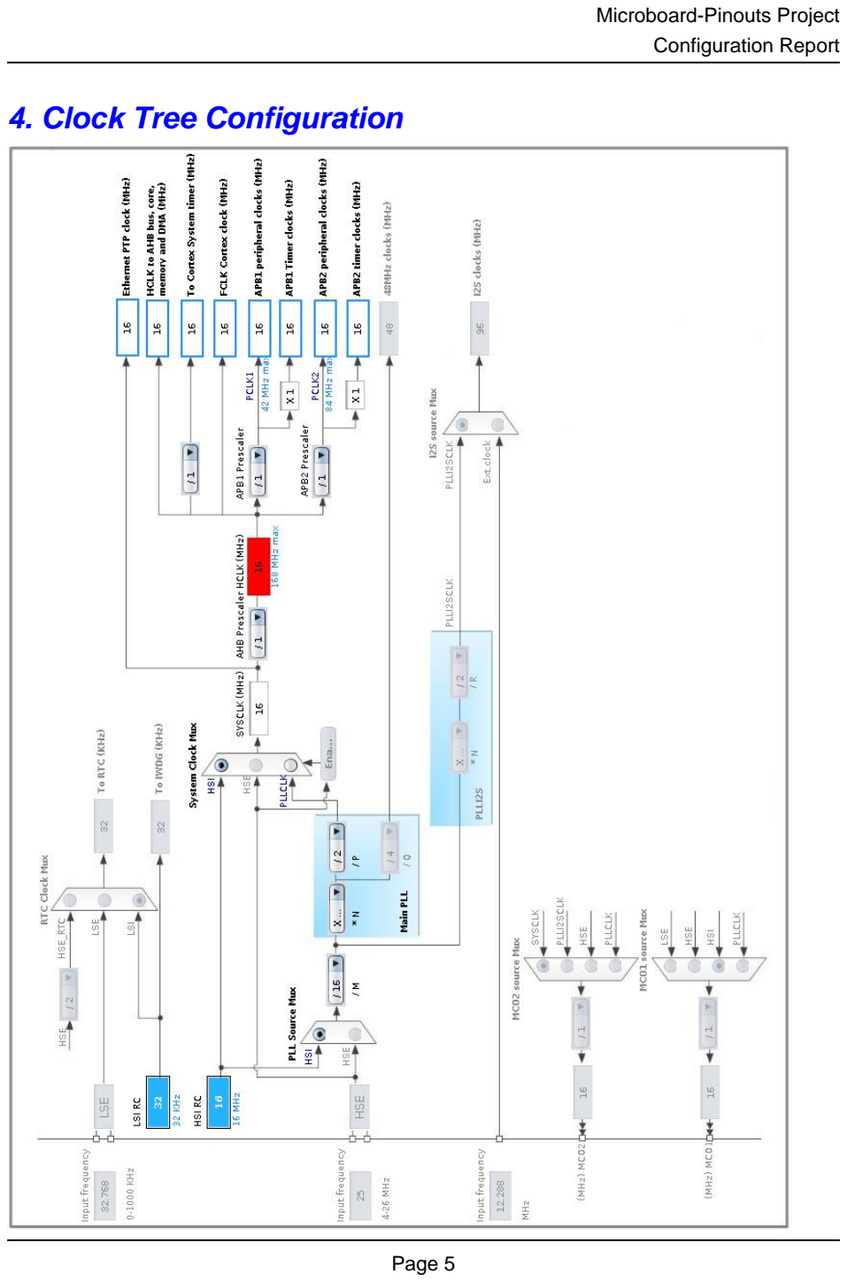
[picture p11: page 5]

# 5. IPs and Middleware Configuration

# 5.1. CAN1

## mode: Mode

## 5.1.1. Parameter Settings:

### Bit Timings Parameters:

Prescaler (for Time Quantum) | 16
Time Quantum | 1000.0 *
Time Quanta in Bit Segment 1 | 1 Time
Time Quanta in Bit Segment 2 | 1 Time
Time for one Bit | 3000 *
ReSynchronization Jump Width | 1 Time

### Basic Parameters:

Time Triggered Communication Mode | Disable
Automatic Bus-Off Management | Disable
Automatic Wake-Up Mode | Disable
No-Automatic Retransmission | Disable
Receive Fifo Locked Mode | Disable
Transmit Fifo Priority | Disable

### Advanced Parameters:

Operating Mode | Normal

# 5.2. CAN2

## mode: Mode

## 5.2.1. Parameter Settings:

### Bit Timings Parameters:

Prescaler (for Time Quantum) | 16
Time Quantum | 1000.0 *
Time Quanta in Bit Segment 1 | 1 Time
Time Quanta in Bit Segment 2 | 1 Time
Time for one Bit | 3000 *
ReSynchronization Jump Width | 1 Time

### Basic Parameters:

Time Triggered Communication Mode | Disable
Automatic Bus-Off Management | Disable
Automatic Wake-Up Mode | Disable
No-Automatic Retransmission | Disable
Receive Fifo Locked Mode | Disable
Transmit Fifo Priority | Disable

### Advanced Parameters:

Operating Mode | Normal

# 5.3. DAC

## mode: OUT1 Configuration

## 5.3.1. Parameter Settings:

### DAC Out1 Settings:

Output Buffer | Enable
Trigger | None

# 5.4. ETH

## Mode: RMII

## 5.4.1. Parameter Settings:

### Advanced : Ethernet Media Configuration:

Auto Negotiation | Enabled

### General : Ethernet Configuration:

Ethernet MAC Address | 00:80:E1:00:00:00
PHY Address | 1

### Ethernet Basic Configuration:

Rx Mode | Polling Mode
TX IP Header Checksum Computation | By hardware

## 5.4.2. Advanced Parameters:

### External PHY Configuration:

PHY Reset delay these values are based on a 1 ms Systick interrupt | 0x000000FF *
PHY Configuration delay | 0x00000FFF *
PHY Read TimeOut | 0x0000FFFF *
PHY Write TimeOut | 0x0000FFFF *

### Common : External PHY Configuration:

Transceiver Basic Control Register | 0x00 *
Transceiver Basic Status Register | 0x01 *
PHY Reset | 0x8000 *
Select loop-back mode | 0x4000 *
Set the full-duplex mode at 100 Mb/s | 0x2100 *
Set the half-duplex mode at 100 Mb/s | 0x2000 *
Set the full-duplex mode at 10 Mb/s | 0x0100 *
Set the half-duplex mode at 10 Mb/s | 0x0000 *
Enable auto-negotiation function | 0x1000 *
Restart auto-negotiation function | 0x0200 *
Select the power down mode | 0x0800 *
Isolate PHY from MII | 0x0400 *
Auto-Negotiation process completed | 0x0020 *
Valid link established | 0x0004 *
Jabber condition detected | 0x0002 *

### Extended : External PHY Configuration:

PHY status register Offset | 0x10 *
MII Interrupt Control Register | 0x11 *
MII Interrupt Status and Misc. Control Register | 0x12 *
PHY Link mask | 0x0001 *
PHY Speed mask | 0x0002 *
PHY Duplex mask | 0x0004 *
PHY Enable interrupts | 0x0002 *
PHY Enable output interrupt events | 0x0001 *
Enable Interrupt on change of link status | 0x0020 *
HY link status interrupt mask | 0x2000 *

# 5.5. I2C1

## I2C: I2C

## 5.5.1. Parameter Settings:

### Master Features:

I2C Speed Mode | Standard Mode
I2C Clock Speed (Hz) | 100000

### Slave Features:

Clock No Stretch Mode | Disabled
Primary Address Length selection | 7-bit
Dual Address Acknowledged | Disabled
Primary slave address | 0
General Call address detection | Disabled

# 5.6. I2C3

## I2C: I2C

## 5.6.1. Parameter Settings:

### Master Features:

I2C Speed Mode | Standard Mode
I2C Clock Speed (Hz) | 100000

### Slave Features:

Clock No Stretch Mode | Disabled
Primary Address Length selection | 7-bit
Dual Address Acknowledged | Disabled
Primary slave address | 0
General Call address detection | Disabled

# 5.7. TIM2

## Channel1: PWM Generation CH1

## 5.7.1. Parameter Settings:

### Counter Settings:

Prescaler (PSC - 16 bits value) | 0

Counter Mode | Up
Counter Period (AutoReload Register - 32 bits value ) | 0
Internal Clock Division (CKD) | No Division

### Trigger Output (TRGO) Parameters:

Master/Slave Mode | Disable (no sync between this TIM (Master) and its Slaves
Trigger Event Selection | Reset (UG bit from TIMx_EGR)

### PWM Generation Channel 1:

Mode | PWM mode 1
Pulse (32 bits value) | 0
Fast Mode | Disable
CH Polarity | High

# 5.8. TIM5

## mode: Clock Source Channel1: PWM Generation CH1 Channel4: PWM Generation CH4

## 5.8.1. Parameter Settings:

### Counter Settings:

Prescaler (PSC - 16 bits value) | 0
Counter Mode | Up
Counter Period (AutoReload Register - 32 bits value ) | 0
Internal Clock Division (CKD) | No Division

### Trigger Output (TRGO) Parameters:

Master/Slave Mode | Disable (no sync between this TIM (Master) and its Slaves
Trigger Event Selection | Reset (UG bit from TIMx_EGR)

### PWM Generation Channel 1:

Mode | PWM mode 1
Pulse (32 bits value) | 0
Fast Mode | Disable
CH Polarity | High

### PWM Generation Channel 4:

Mode | PWM mode 1
Pulse (32 bits value) | 0
Fast Mode | Disable
CH Polarity | High

### * User modified value

# 6. System Configuration

# 6.1. GPIO configuration

IP | Pin | Signal | GPIO mode | GPIO pull/up pull down | Max Speed | User Label
CAN1 | PA11 | CAN1_RX | Alternate Function Push Pull | No pull-up and no pull-down | High *
| PA12 | CAN1_TX | Alternate Function Push Pull | No pull-up and no pull-down | High *
CAN2 | PB5 | CAN2_RX | Alternate Function Push Pull | No pull-up and no pull-down | High *
| PB6 | CAN2_TX | Alternate Function Push Pull | No pull-up and no pull-down | High *
DAC | PA4 | DAC_OUT1 | Analog mode | No pull-up and no pull-down | n/a | Sonar DAC
ETH | PC1 | ETH_MDC | Alternate Function Push Pull | No pull-up and no pull-down | High *
| PA1 | ETH_REF_CLK | Alternate Function Push Pull | No pull-up and no pull-down | High *
| PA2 | ETH_MDIO | Alternate Function Push Pull | No pull-up and no pull-down | High *
| PA7 | ETH_CRS_DV | Alternate Function Push Pull | No pull-up and no pull-down | High *
| PC4 | ETH_RXD0 | Alternate Function Push Pull | No pull-up and no pull-down | High *
| PC5 | ETH_RXD1 | Alternate Function Push Pull | No pull-up and no pull-down | High *
| PB11 | ETH_TX_EN | Alternate Function Push Pull | No pull-up and no pull-down | High *
| PB12 | ETH_TXD0 | Alternate Function Push Pull | No pull-up and no pull-down | High *
| PB13 | ETH_TXD1 | Alternate Function Push Pull | No pull-up and no pull-down | High *
I2C1 | PB7 | I2C1_SDA | Alternate Function Open Drain | Pull-up | High *
| PB8 | I2C1_SCL | Alternate Function Open Drain | Pull-up | High *
I2C3 | PC9 | I2C3_SDA | Alternate Function Open Drain | Pull-up | High *
| PA8 | I2C3_SCL | Alternate Function Open Drain | Pull-up | High *
TIM2 | PA5 | TIM2_CH1 | Alternate Function Push Pull | No pull-up and no pull-down | Low | Sonar PWM
TIM5 | PA0-WKUP | TIM5_CH1 | Alternate Function Push Pull | No pull-up and no pull-down | Low | Main Camera Servo Motor PWM
| PA3 | TIM5_CH4 | Alternate Function Push Pull | No pull-up and no pull-down | Low | Alt Camera Servo Motor PWM
GPIO | PD11 | GPIO_Output | Output Push Pull | No pull-up and no pull-down | Low | LED4
| PD12 | GPIO_Output | Output Push Pull | No pull-up and no pull-down | Low | LED3
| PD13 | GPIO_Input | Input mode | No pull-up and no pull-down | n/a | LED2
| PD14 | GPIO_Output | Output Push Pull | No pull-up and no pull-down | Low | LED1

# 6.2. DMA configuration

## nothing configured in DMA service

# 6.3. NVIC configuration

Interrupt Table | Enable | Preenmption Priority | SubPriority
System tick timer | true | 0 | 0
Non maskable interrupt | unused
Memory management fault | unused
Pre-fetch fault, memory access fault | unused
Undefined instruction or illegal state | unused
Debug monitor | unused
PVD interrupt through EXTI line 16 | unused
Flash global interrupt | unused
RCC global interrupt | unused
CAN1 TX interrupts | unused
CAN1 RX0 interrupts | unused
CAN1 RX1 interrupt | unused
CAN1 SCE interrupt | unused
TIM2 global interrupt | unused
I2C1 event interrupt | unused
I2C1 error interrupt | unused
TIM5 global interrupt | unused
TIM6 global interrupt, DAC1 and DAC2 underrun error interrupts | unused
Ethernet global interrupt | unused
Ethernet wake-up interrupt through EXTI line 19 | unused
CAN2 TX interrupts | unused
CAN2 RX0 interrupts | unused
CAN2 RX1 interrupt | unused
CAN2 SCE interrupt | unused
I2C3 event interrupt | unused
I2C3 error interrupt | unused

### * User modified value

# 7. Power Plugin report

## 7.1. Microcontroller Selection

Series | STM32F4
Line | STM32F407/417
MCU | STM32F407VGTx
Datasheet | 022152_Rev5

## 7.2. Parameter Selection

Temperature | 25
Vdd | 3.3

# 8. Software Project

## 8.1. Project Settings

Name | Value
Project Name | Microboard-Pinouts
Project Folder | /home/lukeinator/Documents/Microboard-Pinouts
Toolchain / IDE | EWARM
Firmware Package Name and Version | STM32Cube FW_F4 V1.9.0

## 8.2. Code Generation Settings

Name | Value
STM32Cube Firmware Library Package | Copy all used libraries into the project folder
Generate peripheral initialization as a pair of '.c/.h' files | No
Backup previously generated files when re-generating | No
Delete previously generated files when not re-generated | Yes
Set all free pins as analog (to optimize the power consumption) | No

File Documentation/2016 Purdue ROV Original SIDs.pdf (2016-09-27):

# Power System Interconnection Diagram (SID)

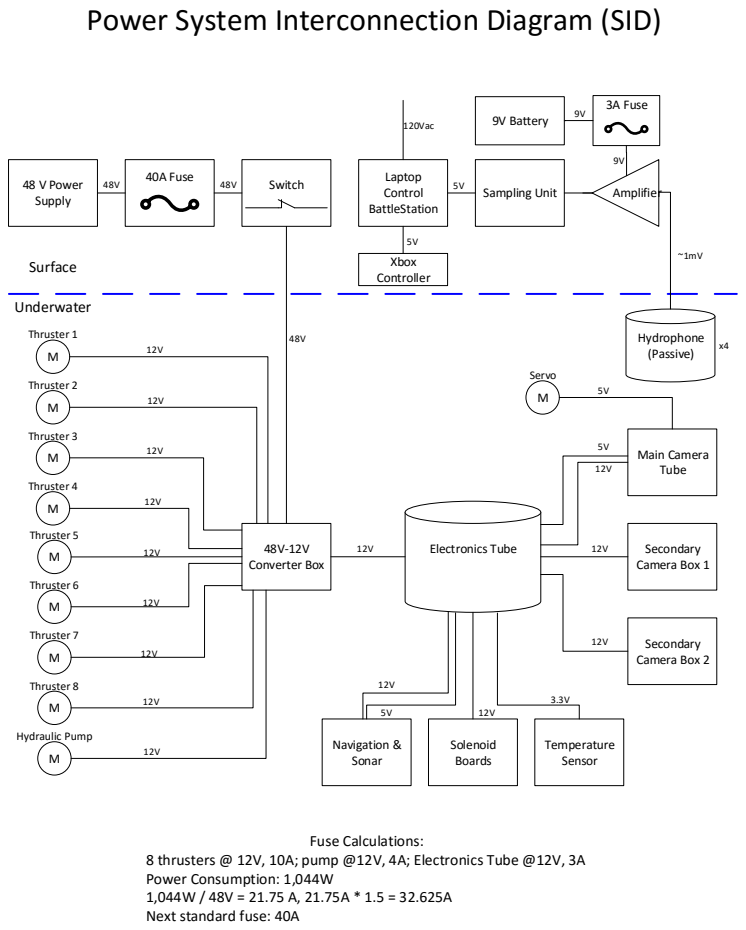
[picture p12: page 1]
48 V Power Supply; 40A Fuse; Laptop; Control BattleStation; Sampling Unit; 48V-12V Converter Box; Thruster 1; Thruster 2; Thruster 3; Thruster 4; Thruster 5; Thruster 6; Thruster 7; Thruster 8; Hydraulic Pump; Electronics Tube; Secondary Camera Box 1; Main Camera Tube; Secondary Camera Box 2; Hydrophone (Passive); Switch; 120Vac; 9V Battery; Surface; Underwater; Fuse Calculations:; Xbox Controller; Servo; 3A Fuse; Amplifier

Navigation & Sonar | Solenoid Boards | Temperature Sensor

8 thrusters @ 12V, 10A; pump @12V, 4A; Electronics Tube @12V, 3A
Power Consumption: 1,044W
Next standard fuse: 40A

# Data System Interconnection Diagram (SID)

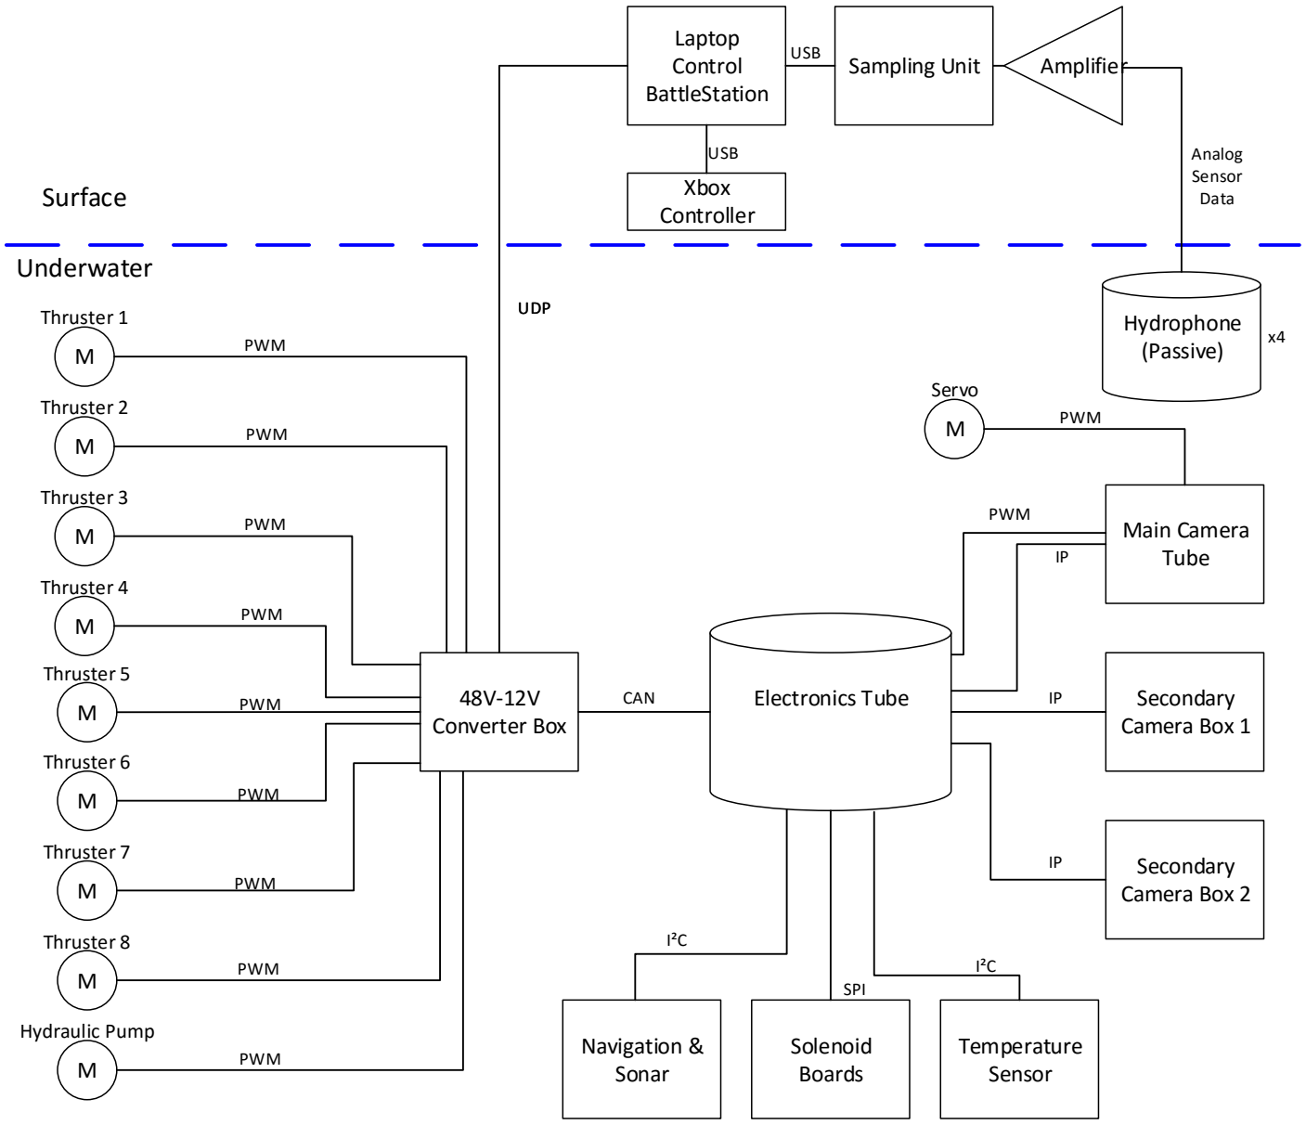
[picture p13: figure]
Laptop Control BattleStation; Sampling Unit; Amplifier; 48V-12V Converter Box; Thruster 1; Thruster 2; Thruster 3; Thruster 4; Thruster 5; Thruster 6; Thruster 7; Thruster 8; Hydraulic Pump; Electronics Tube; Navigation & Sonar; Solenoid Boards; Temperature Sensor; Secondary Camera Box 1; Main Camera Tube; Secondary Camera Box 2; PWM; Hydrophone (Passive); USB; CAN; I²C; SPI; Surface; Underwater; Xbox Controller; UDP; Servo; Analog Sensor Data

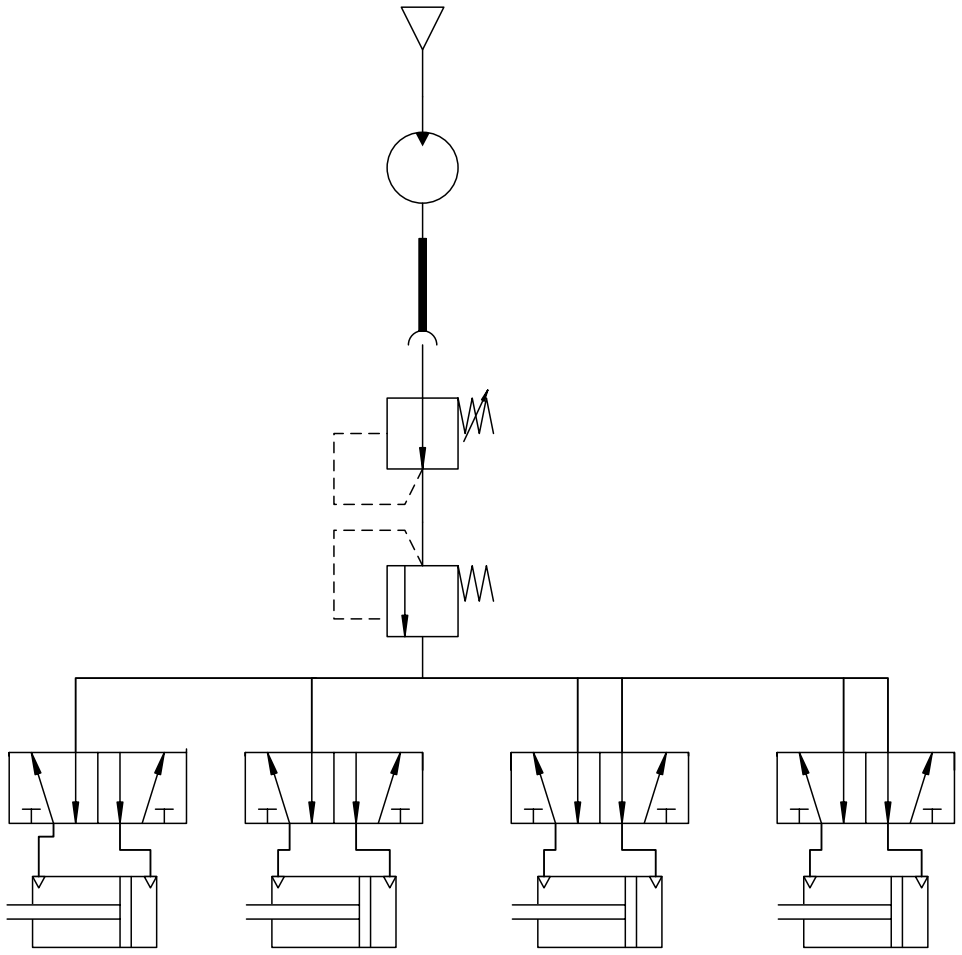
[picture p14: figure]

Manipulator Grasper

Solenoids

Pressure Regulator

Hydraulic Pump

Adapter

Wellhead

Pressure Release Valve

Manipulator Rotator | ESP Claw

### Entire System Underwater

# Fluids (Hydraulics) System Interconnection Diagram (SID)

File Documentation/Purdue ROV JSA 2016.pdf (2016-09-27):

Safety Information for the Proven Robotics ROV

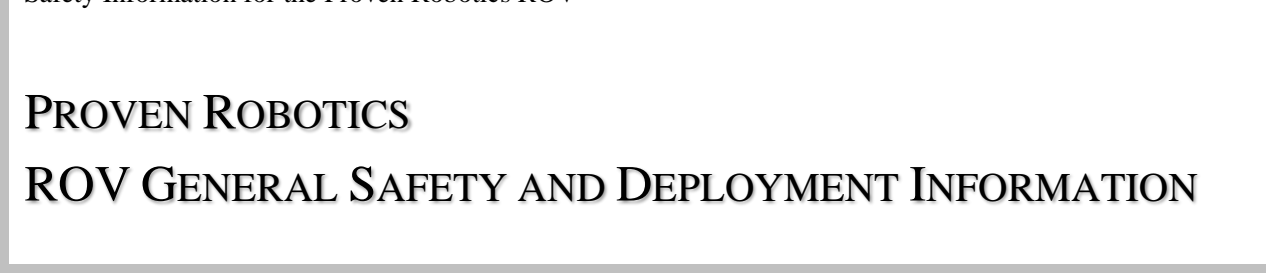
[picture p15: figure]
PROVEN ROBOTICS

## ROV GENERAL SAFETY AND DEPLOYMENT INFORMATION

TASK | HAZARDS | CONTROLS
1. Deploying ROV | Deep Water (drowning) | Ensure no obstacles near deployment. Only allow hands and arms in water. Must have good balance and secure footings.
2. Connect Tether to ROV | Caught Hands / Limbs | Ensure all connections are secure. No loops large enough to catch limbs upon deployment.
3. Connect Tether to Communication Equipment | Tripping, Electrocution | Ensure all cables are securely attached to table or other anchor point. All hands off vehicle during initial power-on.
4. Retrieval of ROV | Back Strain | Never retrieve alone, always use two people. Kneel down to ensure one neither over-stretches or bends down too far.

Required Training:
Emergency shutdown procedure
Proper deployment and retrieval techniques

Required Personal Protective Equipment (PPE) Safety Glasses
Closed-toe shoes
Non-slip shoes
Contributors: | Jared Borg, Mechanical Team
Created: | May 22, 2016

Template from UC Berkeley, 317 University Hall #1150, Berkeley, CA 94720-1150
(510) 642-3073 ● http://www.ehs.berkeley.edu

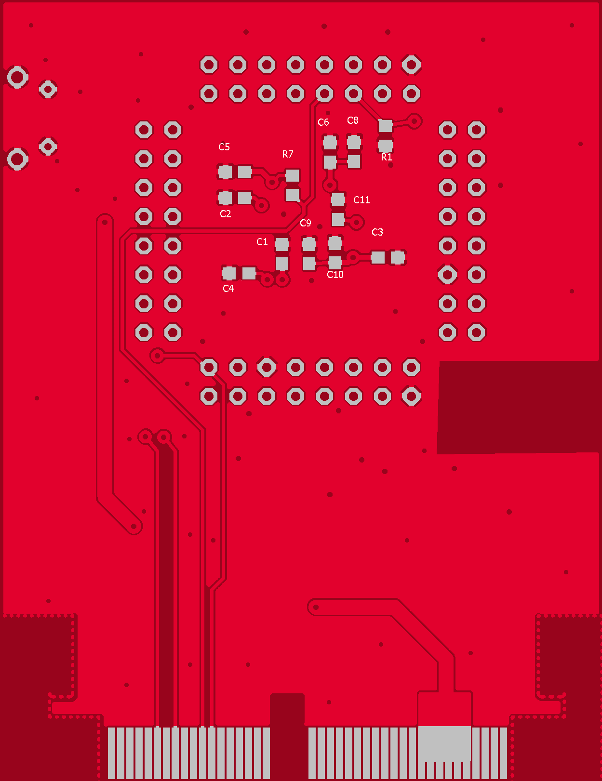
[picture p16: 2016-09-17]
Electronics/Application-PCB/eagleUp/eagleUp_Application_board_bottom.png

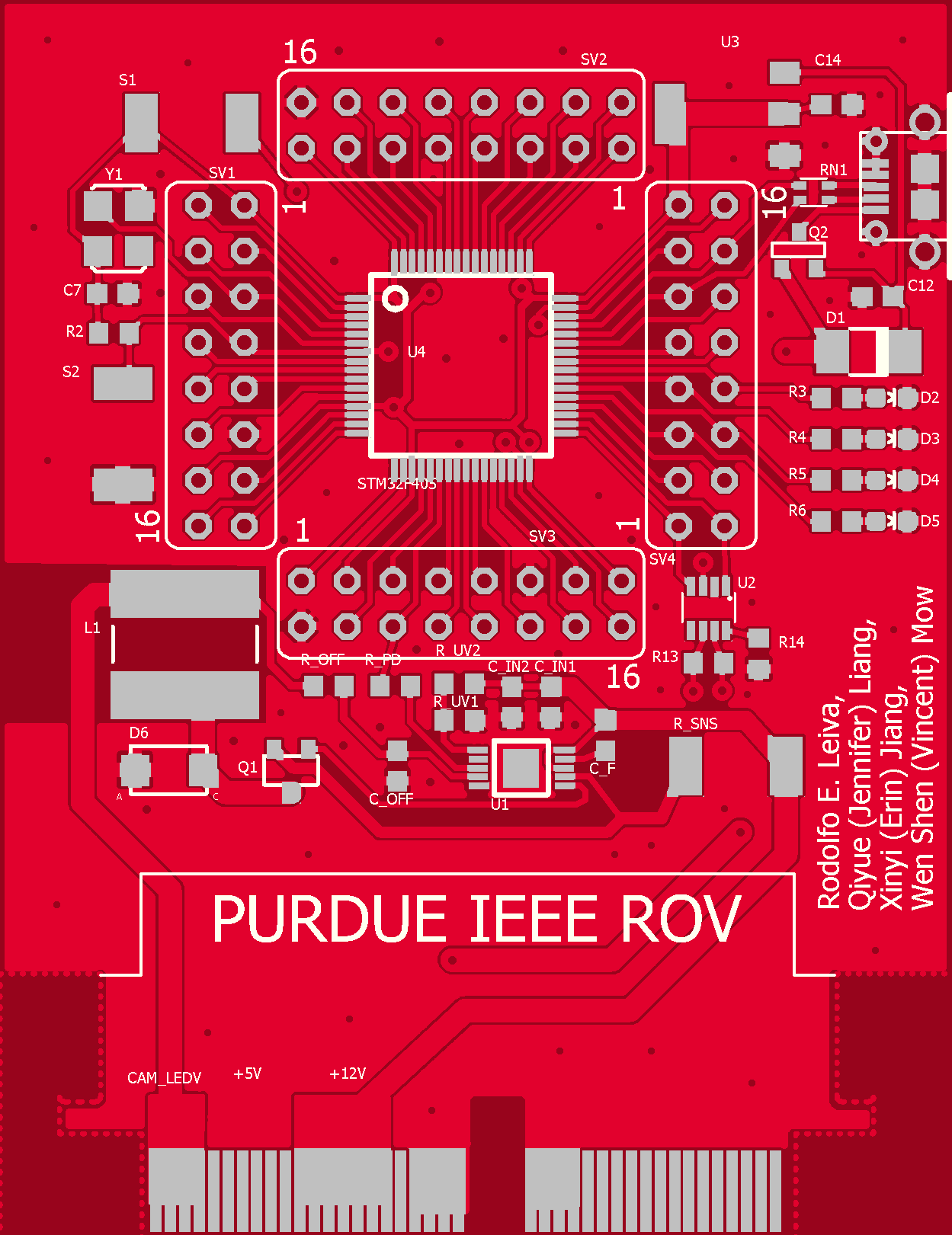
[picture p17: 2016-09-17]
Electronics/Application-PCB/eagleUp/eagleUp_Application_board_top.png

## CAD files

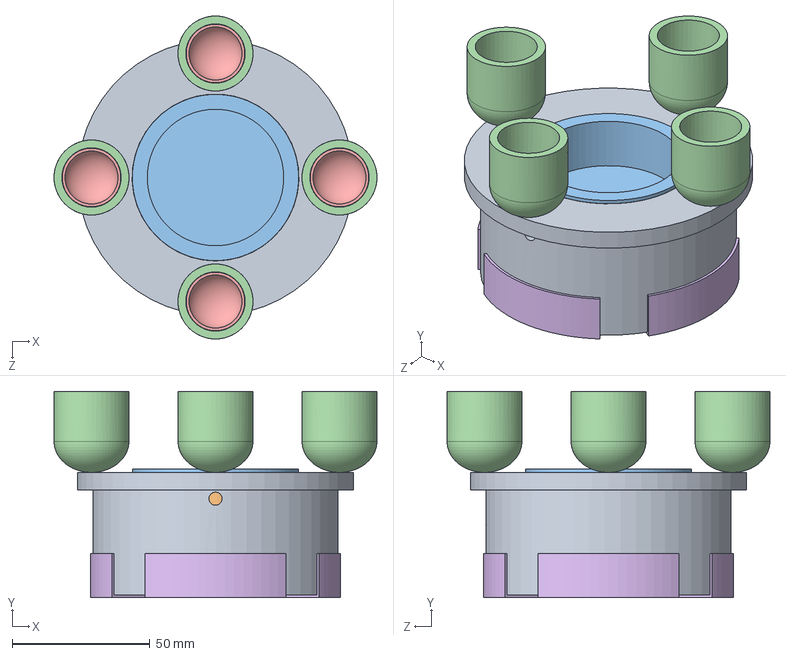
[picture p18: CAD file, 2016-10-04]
Mechanical/Mission Props (MATE)/EXPLORER FINAL ASSEMBLIES/WELLHEAD CAP.SLDASM
117.2 x 74.9 x 117.2 mm
3 X 2 ABS BUSHING (2)
2 PVC PIPE 2CM
2 KNOCKOUT TEST CAP
1-2 PVC CAP x 4
VELCRO F x 4
VELCRO G x 4

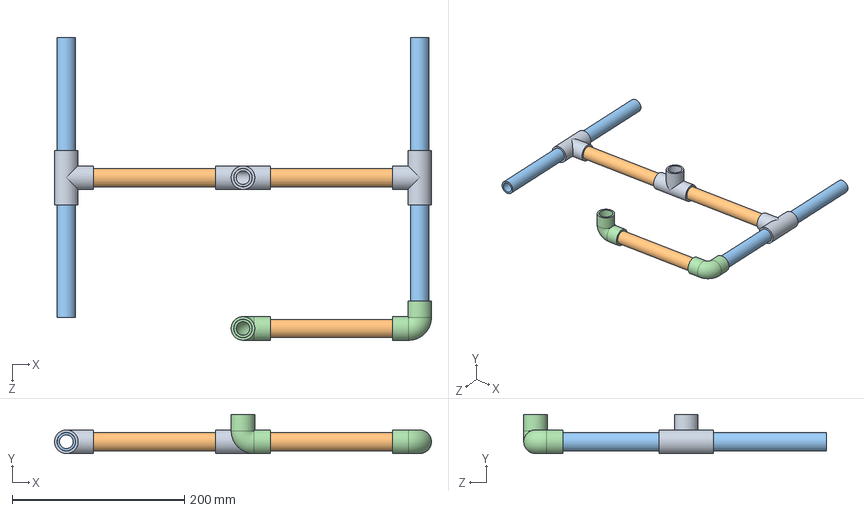
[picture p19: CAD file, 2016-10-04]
Mechanical/Mission Props (MATE)/SUB-ASSEMBLIES/PARAMURICE CORAL BASE.SLDASM
438.3 x 45.5 x 351.9 mm
1-2 PVC TEE x 3
1-2 PVC PIPE 18CM x 3
1-2 PVC PIPE 15CM x 4
1-2 PVC ELBOW x 2

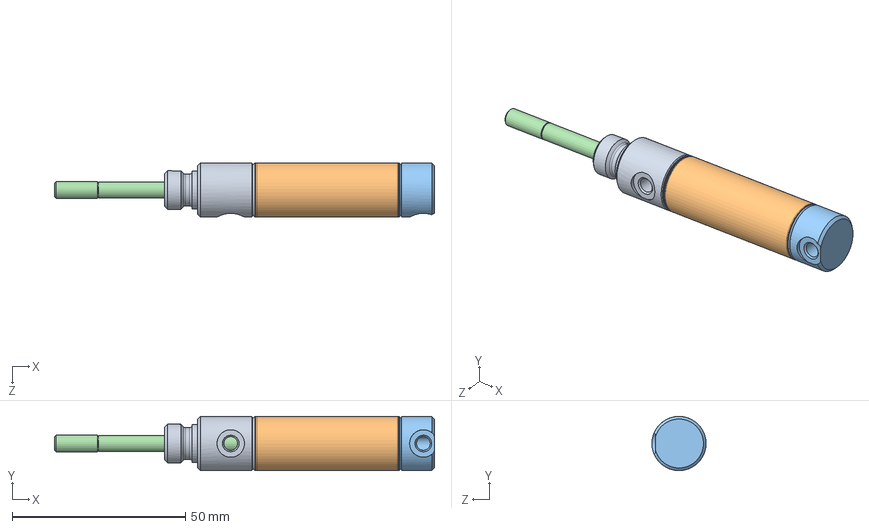
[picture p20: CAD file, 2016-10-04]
Mechanical/ROV Part Library/Hydraulics + Pneumatics/Hydraulic Cylinders/HL-020.75-DQ/HL-020_75-DQ.sldasm
109.5 x 15.6 x 15.6 mm
02RQ000-0_rod_guide
02R-1_6380
02PQ0000_rear_head
HL-020_75-DQ0_rod

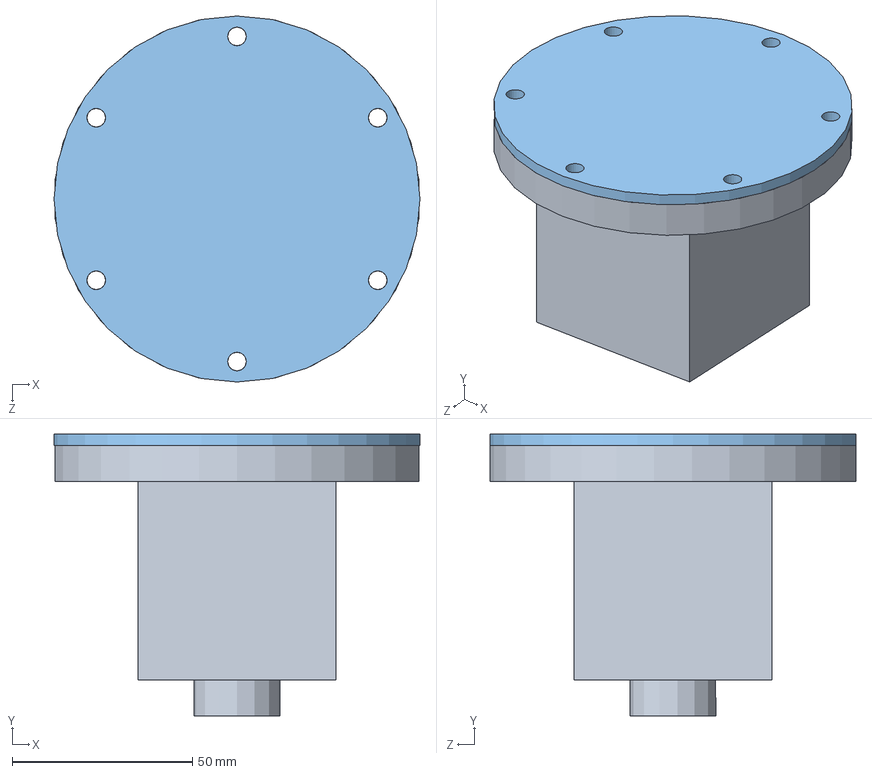
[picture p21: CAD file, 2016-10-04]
Mechanical/Secondary Camera Box/Secondary Camera Box Assembly.SLDASM
101.6 x 78.2 x 101.6 mm
Secondary Camera Box
IP board camera IPR1665X-L6
Secondary Camera Box view port

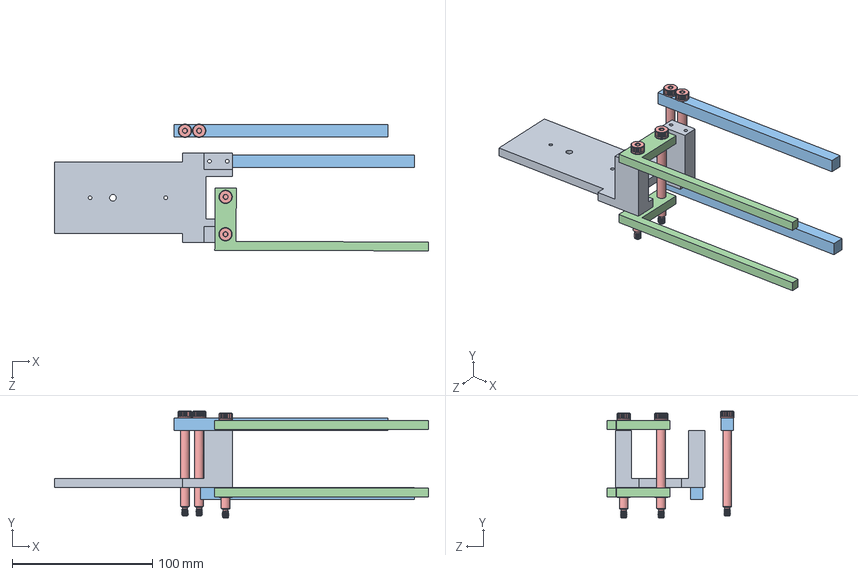
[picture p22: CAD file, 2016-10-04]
Mechanical/ESP Tool/Final ESP Claw Assembly.SLDASM
266.7 x 76.1 x 90.4 mm
Baseplate
95606A110 x 6
Claw of stationary part x 2
Claw of moving part x 2
97345A191 x 4

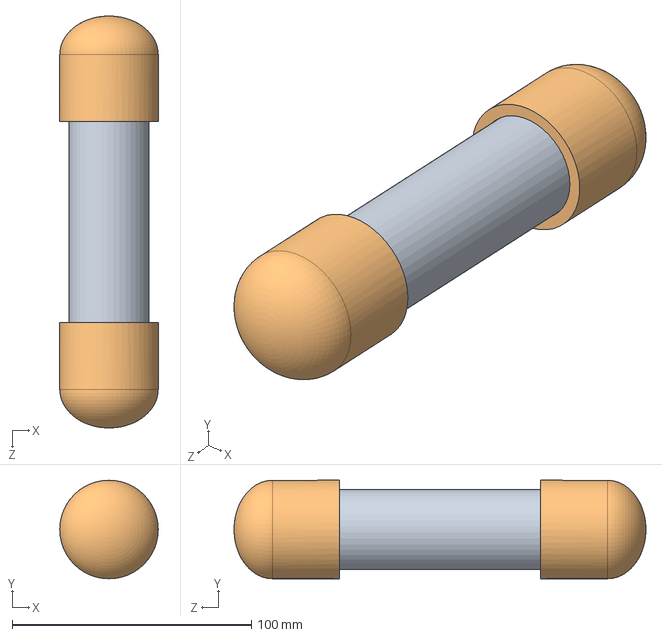
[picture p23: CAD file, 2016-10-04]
Mechanical/Mission Props (MATE)/EXPLORER FINAL ASSEMBLIES/OIL SAMPLE.SLDASM
41.2 x 41.2 x 172.2 mm
1 PVC PIPE 14CM
1 PVC CAP x 2

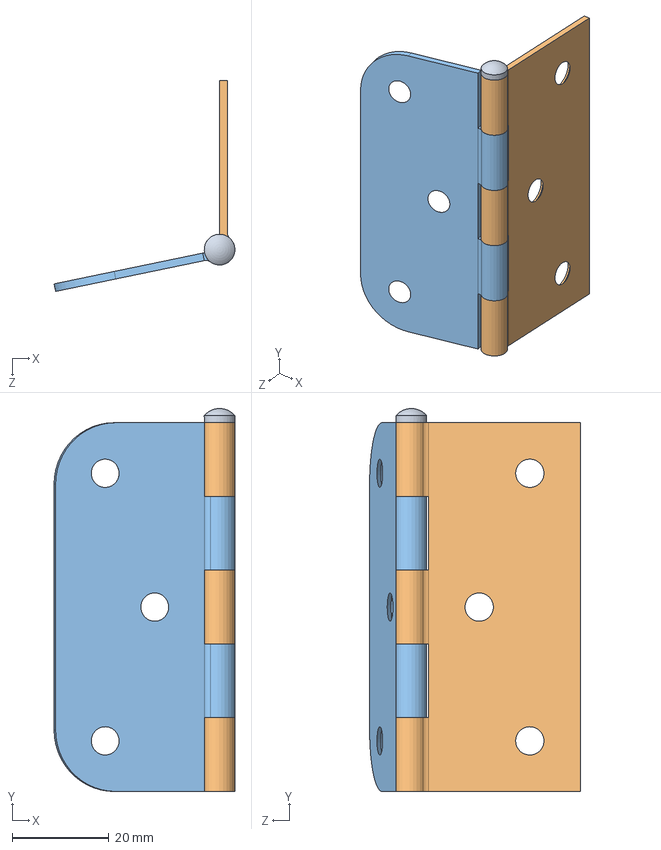
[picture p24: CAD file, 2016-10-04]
Mechanical/Mission Props (MATE)/SUB-ASSEMBLIES/HINGE/Hinge Simple.SLDASM
37.4 x 79.1 x 43.6 mm
Hinge Pin
Hinge Side 1
Hinge Side 2

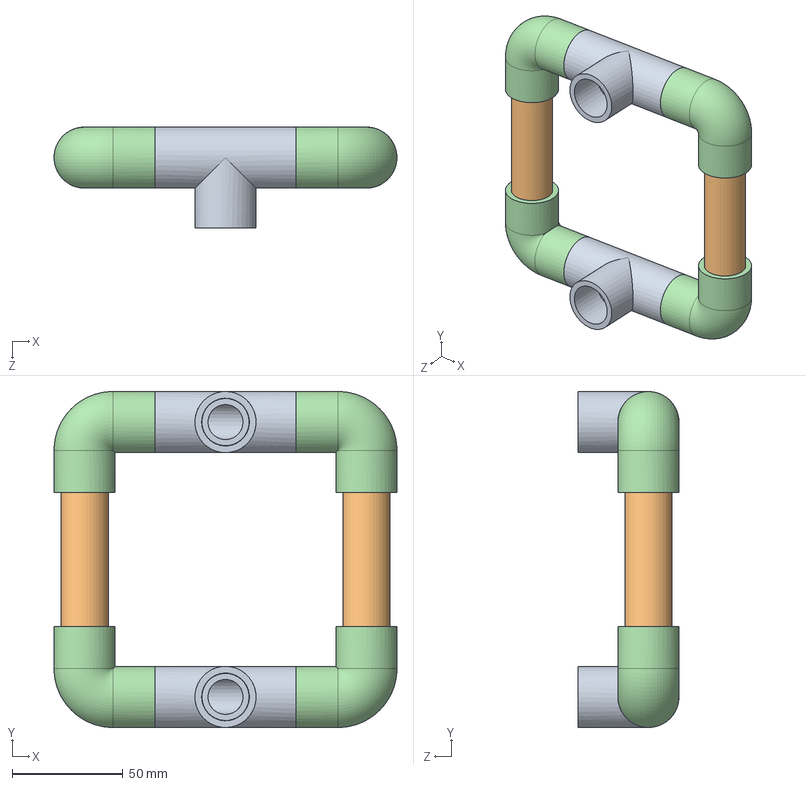
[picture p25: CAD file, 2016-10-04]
Mechanical/Mission Props (MATE)/SUB-ASSEMBLIES/SCOUT CUBE SATS BASE.SLDASM
154.6 x 151.4 x 45.5 mm
1-2 PVC TEE x 2
1-2 PVC PIPE 10CM x 2
1-2 PVC PIPE 3CM x 4
1-2 PVC ELBOW x 4

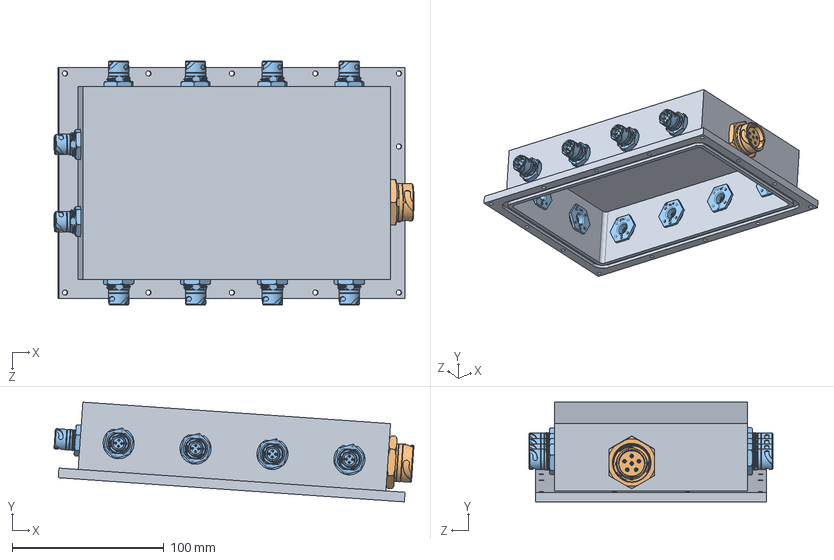
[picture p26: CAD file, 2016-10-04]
Mechanical/Power Distribution Box/PDB Lidless Assembly.SLDASM
237.1 x 65.7 x 160.6 mm
Power Distribution Box & connector holes v1
Samtec ACR 22
Samtec ACR-12 Plastic x 10

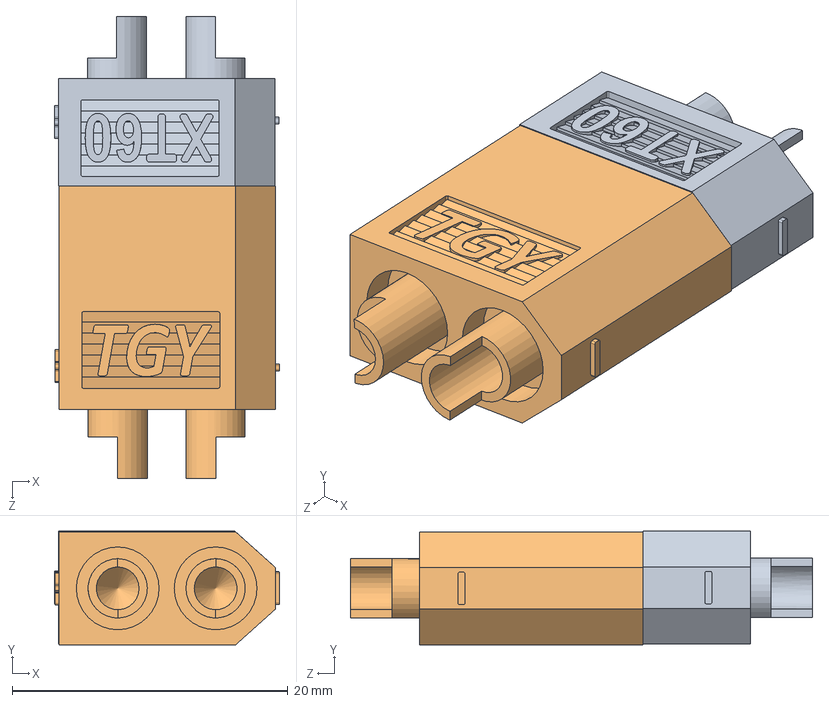
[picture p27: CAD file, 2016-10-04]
Mechanical/ROV Part Library/Electrical Connectors/Standard/XT-60.SLDASM
16.4 x 8.25 x 33.5 mm
XT-60 female
XT-60 male

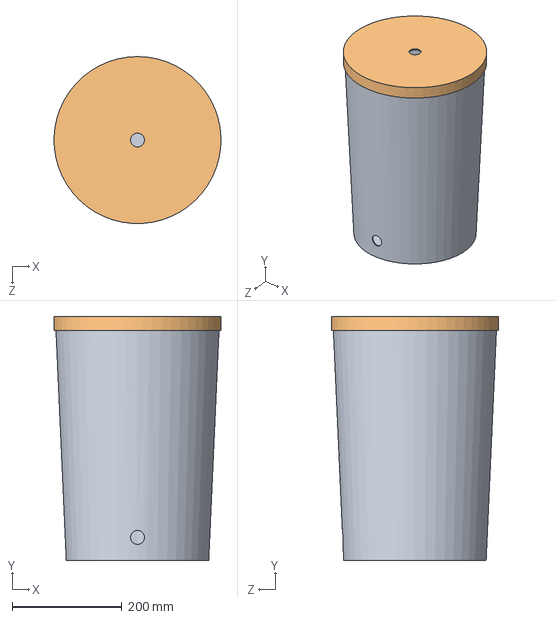
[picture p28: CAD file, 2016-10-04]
Mechanical/Mission Props (MATE)/SUB-ASSEMBLIES/VENT BUCKET.SLDASM
304.7 x 445.3 x 304.5 mm
5 GALLON BUCKET BASE
5 GALLON BUCKET LID

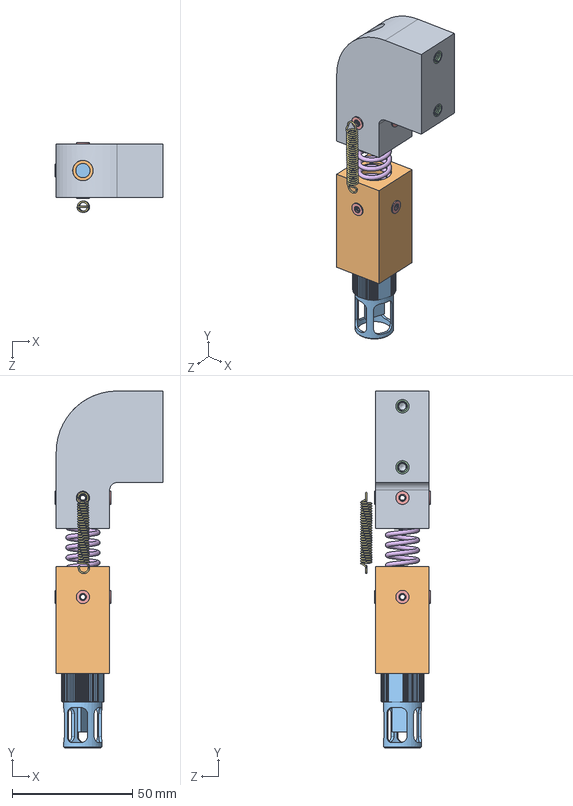
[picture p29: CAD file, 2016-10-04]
Mechanical/Temperature Probe/A. Temperature Probe.SLDASM
45.0 x 148.6 x 29.0 mm
Base Block
Sensor Block
Blue Robotics Temperature Sensor
8-32 Press-Fit Plastic 692394A114 x 2
4-40 Press-Fit Plastic Flange 95110A110 x 8
Compression Spring 1986K124
Extension Spring

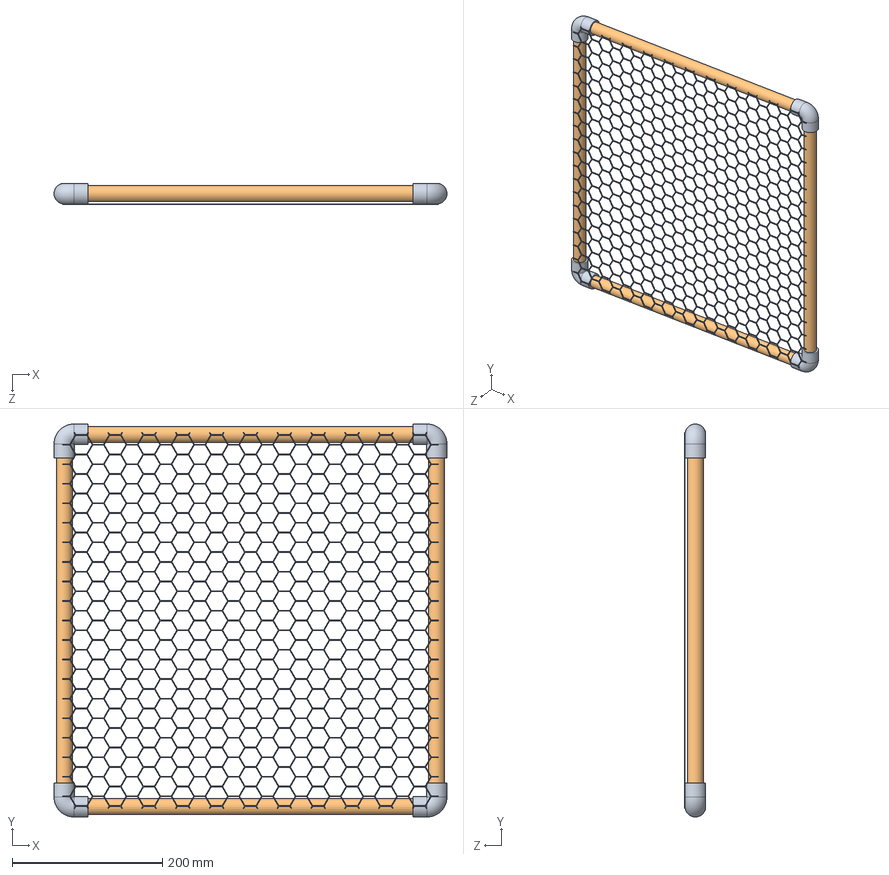
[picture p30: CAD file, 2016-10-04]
Mechanical/Mission Props (MATE)/EXPLORER FINAL ASSEMBLIES/ENVIRONMENTAL ELEVATOR.SLDASM
523.0 x 523.0 x 28.6 mm
1-2 PVC ELBOW x 4
1-2 PVC PIPE 47CM x 4
MESH A

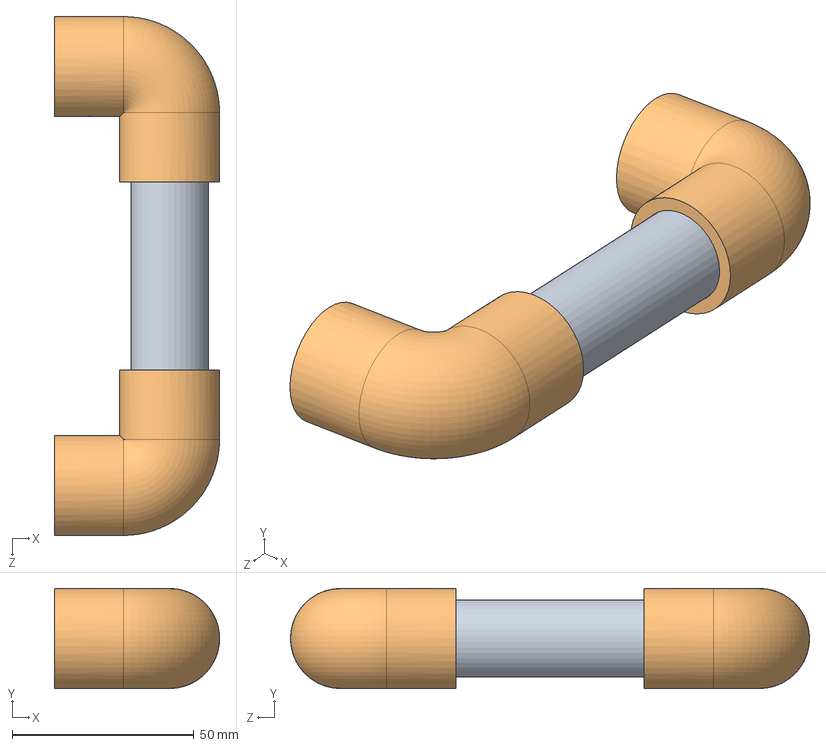
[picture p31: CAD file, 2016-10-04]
Mechanical/Mission Props (MATE)/SUB-ASSEMBLIES/HANDLE.SLDASM
45.5 x 27.6 x 143.0 mm
1-2 PVC PIPE 9CM
1-2 PVC ELBOW x 2

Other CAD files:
Mechanical/A. X8.SLDASM
Mechanical/Power Distribution Box/Power Distribution Box Assembly.SLDASM
Mechanical/Power Distribution Box/Power Distribution Box Welded/A. Power Distribution Box Welded.SLDASM
Mechanical/Wellhead/A. Wellhead Tool Assembly.SLDASM
Mechanical/ESP Tool/Baseplate.SLDPRT
Mechanical/ESP Tool/Claw of moving part.SLDPRT
Mechanical/ESP Tool/Claw of stationary part.SLDPRT
Mechanical/Electronics Tube/1.sldprt
Mechanical/Electronics Tube/2_1.sldprt
Mechanical/Electronics Tube/A. Electronics Tube drawing.SLDDRW
Mechanical/Electronics Tube/A. Electronics Tube.SLDASM
Mechanical/Electronics Tube/CATIA CAM/Front End Cap/End Cap Front stock.CATPart
Mechanical/Electronics Tube/CATIA CAM/Front End Cap/End Cap Front.CATPart
Mechanical/Electronics Tube/CATIA CAM/Front End Cap/end cap front product.CATProduct
Mechanical/Electronics Tube/CATIA CAM/Tube Coupling/Product1.11.CATPart
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

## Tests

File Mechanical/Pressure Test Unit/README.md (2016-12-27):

# Pressure Test Unit

The pressure test unit is made from a polycarbonate tube set into aluminum plates on the top and the bottom. Threaded rods are used to secure the two plates in place. A garden hose using municipal pressure (40 - 60 psi) feeds into the top plate, and provides enough pressure to simulate a depth of 100 meters. A pressure gauge is used to control the pressure inside the chamber. This system was designed to test components at competition depth (at least up to the competition 40 feet), and to test components without going to a pool.

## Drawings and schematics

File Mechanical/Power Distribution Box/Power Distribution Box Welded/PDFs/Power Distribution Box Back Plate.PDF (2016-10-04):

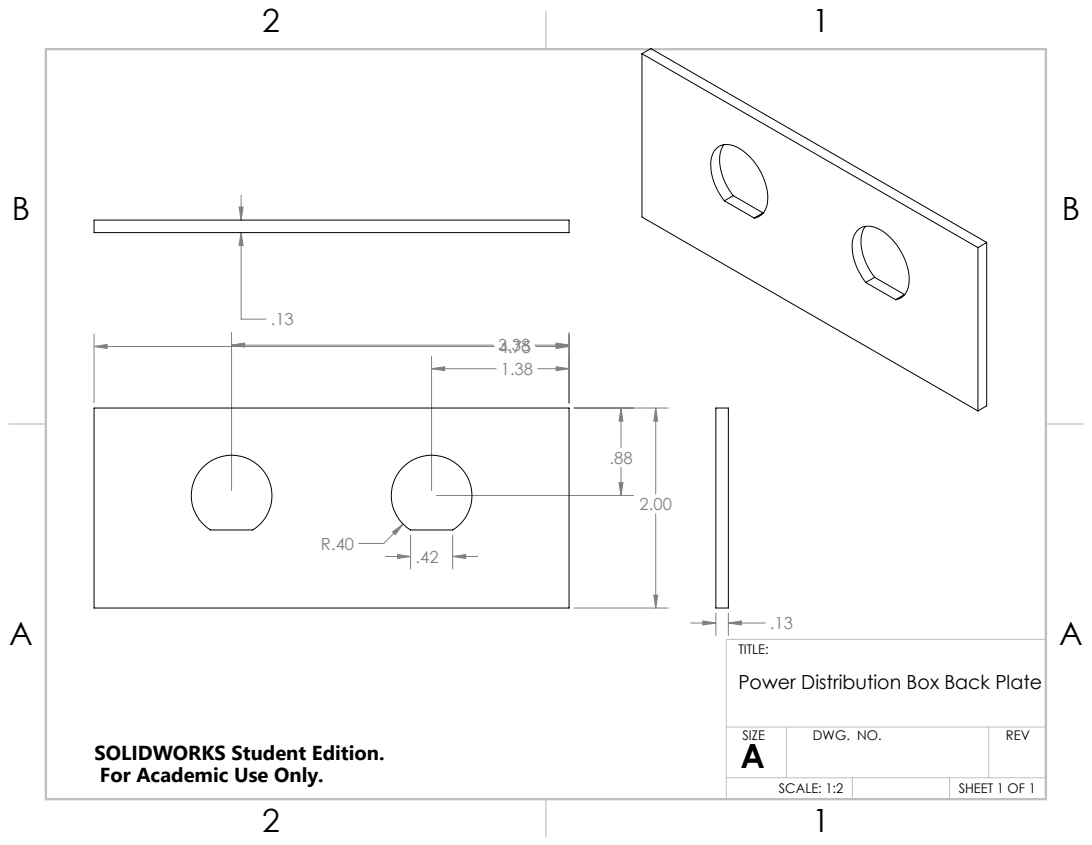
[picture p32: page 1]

TITLE:
Power Distribution Box Back Plate

SIZE A | DWG. NO. | REV

SOLIDWORKS Student Edition.
For Academic Use Only.

SCALE: 1:2 | | SHEET 1 OF 1

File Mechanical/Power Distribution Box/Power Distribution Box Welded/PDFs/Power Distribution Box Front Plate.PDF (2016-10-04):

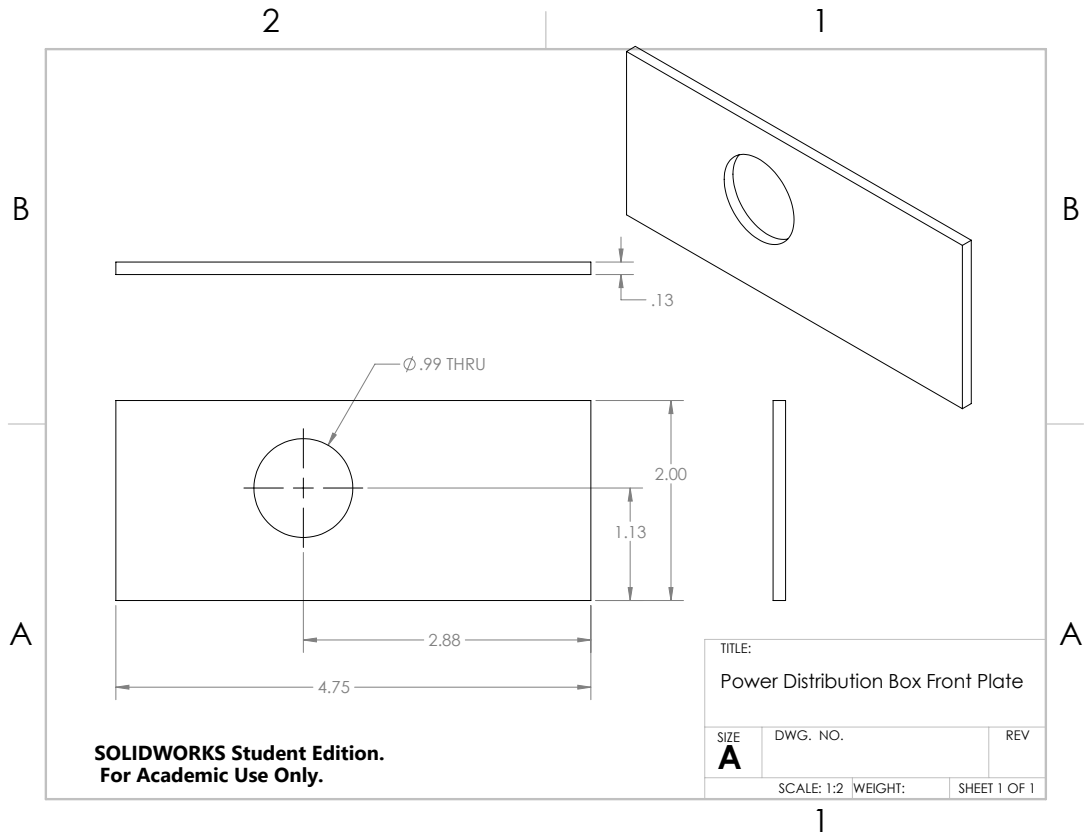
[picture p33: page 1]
.99 THRU

TITLE:
Power Distribution Box Front Plate

SIZE A | DWG. NO. | REV

SOLIDWORKS Student Edition.
For Academic Use Only.

SCALE: 1:2 | WEIGHT: | SHEET 1 OF 1

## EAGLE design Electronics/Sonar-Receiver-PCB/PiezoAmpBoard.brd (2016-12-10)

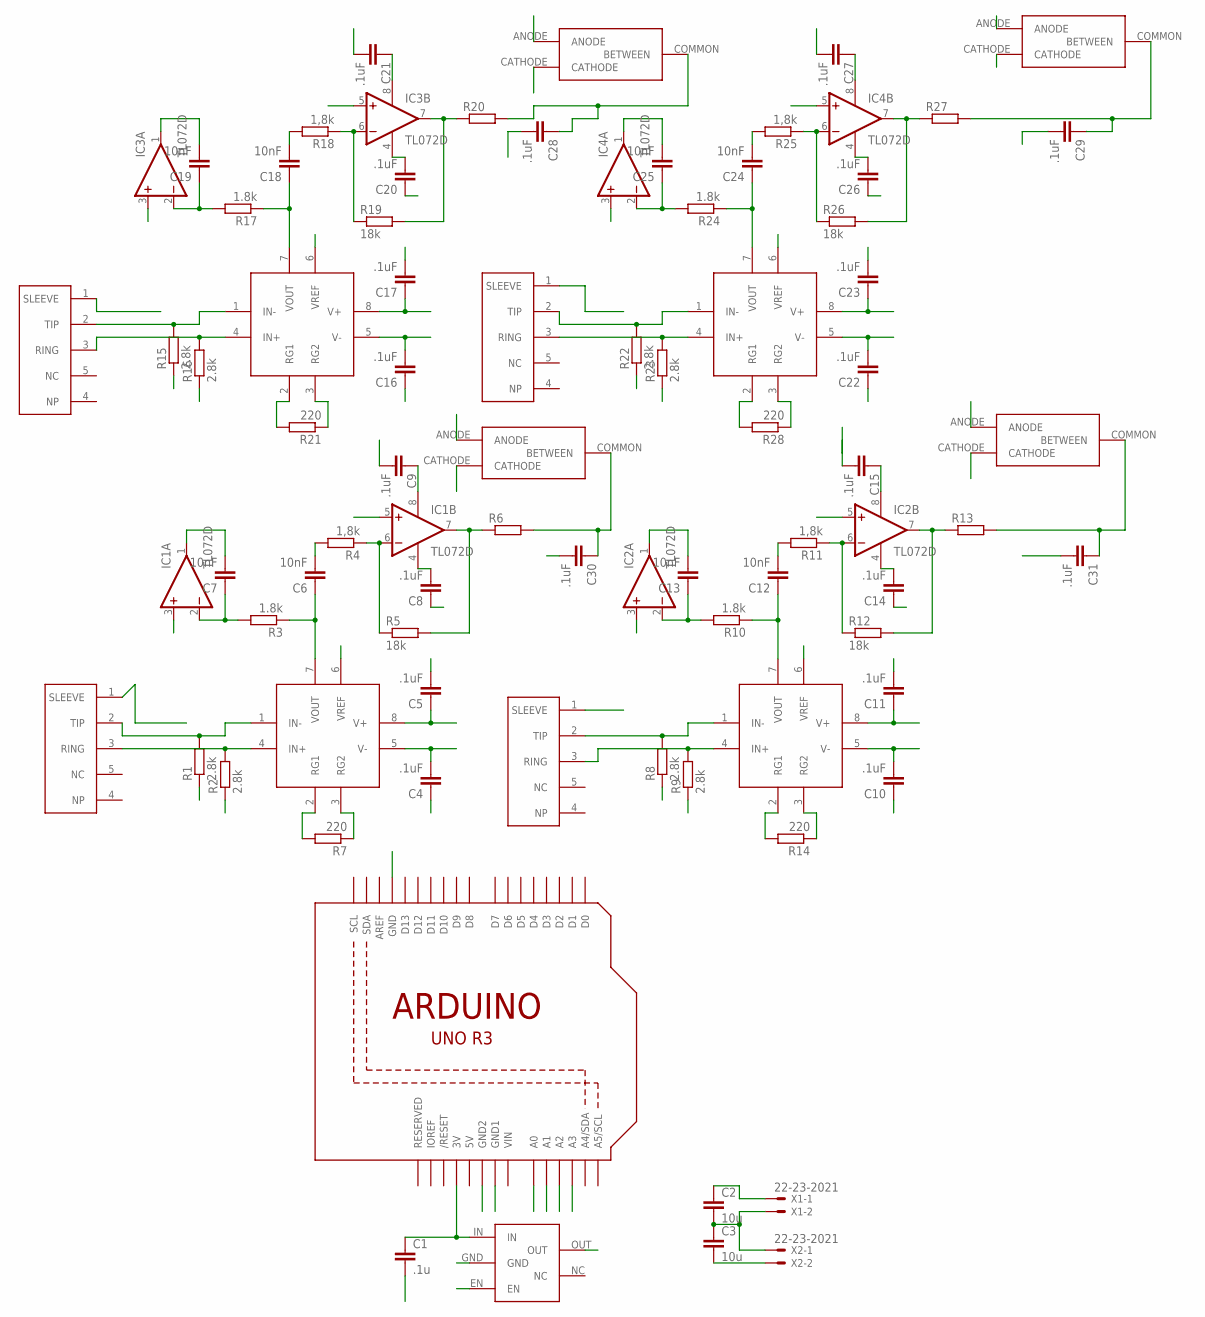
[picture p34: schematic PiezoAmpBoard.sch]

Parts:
C1: .1u; C0603
C2, C3: 10u; C0603
C4, C5, C8, C9, C10, C11, C14, C15, C16, C17, C20, C21, C22, C23, C26, C27, C28, C29, C30, C31: .1uF; C0603
C6, C7, C12, C13, C18, C19, C24, C25: 10nF; C0603
IC1, IC2, IC3, IC4: TL072D; SO08
R1, R2, R8, R9, R15, R16, R22, R23: 2.8k; R0603
R3, R10, R17, R24: 1.8k; R0603
R4, R11, R18, R25: 1,8k; R0603
R5, R12, R19, R26: 18k; R0603
R6, R13, R20, R27: R-EU_R0603; R0603
R7, R14, R21, R28: 220; R0603
U1: ARDUINOR3-BPLACE
U$1: TPS76316; PDSO
U$2, U$3, U$4, U$5: AD82216; SOIC08
U$6, U$7, U$8, U$9: BAV99T; SOT-523
U$10, U$11, U$12, U$13: 3MMJACK; 1X05
X1, X2: 22-23-2021

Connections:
3.3V: C1.1, U1.3V, U$1.EN, U$1.IN, U$6.CATHODE, U$7.CATHODE, U$8.CATHODE, U$9.CATHODE
5V: U1.5V
GND: C1.2, U1.GND, U1.GND1, U1.GND2, U$1.GND, U$6.ANODE, U$7.ANODE, U$8.ANODE, U$9.ANODE
unnamed: R7.2, U$2.2 (RG1)
unnamed: R1.2, U$2.1 (IN-), U$10.2 (TIP)
unnamed: R2.2, U$2.4 (IN+), U$10.3 (RING)
unnamed: R7.1, U$2.3 (RG2)
unnamed: C6.1, R3.1, U$2.7 (VOUT)
unnamed: C7.1, IC1.2 (-IN), R3.2
unnamed: IC1.7 (OUT), R5.2, R6.1
unnamed: R8.2, U$3.1 (IN-), U$13.2 (TIP)
unnamed: C6.2, R4.2
unnamed: IC1.6 (-IN), R4.1, R5.1
unnamed: R9.2, U$3.4 (IN+), U$13.3 (RING)
unnamed: R14.2, U$3.2 (RG1)
unnamed: R14.1, U$3.3 (RG2)
unnamed: C12.1, R10.1, U$3.7 (VOUT)
unnamed: C13.1, IC2.2 (-IN), R10.2
unnamed: IC2.7 (OUT), R12.2, R13.1
unnamed: C12.2, R11.2
unnamed: IC2.6 (-IN), R11.1, R12.1
unnamed: R15.2, U$4.1 (IN-), U$11.2 (TIP)
unnamed: R16.2, U$4.4 (IN+), U$11.3 (RING)
unnamed: R21.2, U$4.2 (RG1)
unnamed: R21.1, U$4.3 (RG2)
unnamed: C18.1, R17.1, U$4.7 (VOUT)
unnamed: C19.1, IC3.2 (-IN), R17.2
unnamed: IC3.7 (OUT), R19.2, R20.1
unnamed: C18.2, R18.2
unnamed: IC3.6 (-IN), R18.1, R19.1
unnamed: R22.2, U$5.1 (IN-), U$12.2 (TIP)
unnamed: R23.2, U$5.4 (IN+), U$12.3 (RING)
unnamed: R28.2, U$5.2 (RG1)
unnamed: R28.1, U$5.3 (RG2)
unnamed: C24.1, R24.1, U$5.7 (VOUT)
unnamed: C25.1, IC4.2 (-IN), R24.2
unnamed: IC4.7 (OUT), R26.2, R27.1
unnamed: C24.2, R25.2
unnamed: IC4.6 (-IN), R25.1, R26.1
PEIZOIN1: C28.1, R20.2, U1.A0, U$6.COMMON (BETWEEN)
PEIZOIN2: C29.1, R27.2, U1.A1, U$7.COMMON (BETWEEN)
PEIZOIN3: C31.1, R13.2, U1.A2, U$9.COMMON (BETWEEN)
PEIZOIN4: C30.1, R6.2, U1.A3, U$8.COMMON (BETWEEN)
VGND: C2.2, C3.1, C4.1, C5.2, C8.1, C9.2, C10.1, C11.2, C14.1, C15.2, C16.1, C17.2, C20.1, C21.2, C22.1, C23.2, C26.1, C27.2, C28.2, C29.2, C30.2, C31.2, IC1.3 (+IN), IC1.5 (+IN), IC2.3 (+IN), IC2.5 (+IN), IC3.3 (+IN), IC3.5 (+IN), IC4.3 (+IN), IC4.5 (+IN), R1.1, R2.1, R8.1, R9.1, R15.1, R16.1, R22.1, R23.1, U$1.OUT, U$10.1 (SLEEVE), U$11.1 (SLEEVE), U$12.1 (SLEEVE), U$13.1 (SLEEVE), X1.2, X2.1
VIN: U1.VIN
VREF: C7.2, IC1.1 (OUT), U$2.6 (VREF)
VREF1: C13.2, IC2.1 (OUT), U$3.6 (VREF)
VREF2: C19.2, IC3.1 (OUT), U$4.6 (VREF)
VREF3: C25.2, IC4.1 (OUT), U$5.6 (VREF)
VS+: C2.1, C5.1, C9.1, C11.1, C15.1, C17.1, C21.1, C23.1, C27.1, IC1.8 (V+), IC2.8 (V+), IC3.8 (V+), IC4.8 (V+), U$2.8 (V+), U$3.8 (V+), U$4.8 (V+), U$5.8 (V+), X1.1
VS-: C3.2, C4.2, C8.2, C10.2, C14.2, C16.2, C20.2, C22.2, C26.2, IC1.4 (V-), IC2.4 (V-), IC3.4 (V-), IC4.4 (V-), U$2.5 (V-), U$3.5 (V-), U$4.5 (V-), U$5.5 (V-), X2.2

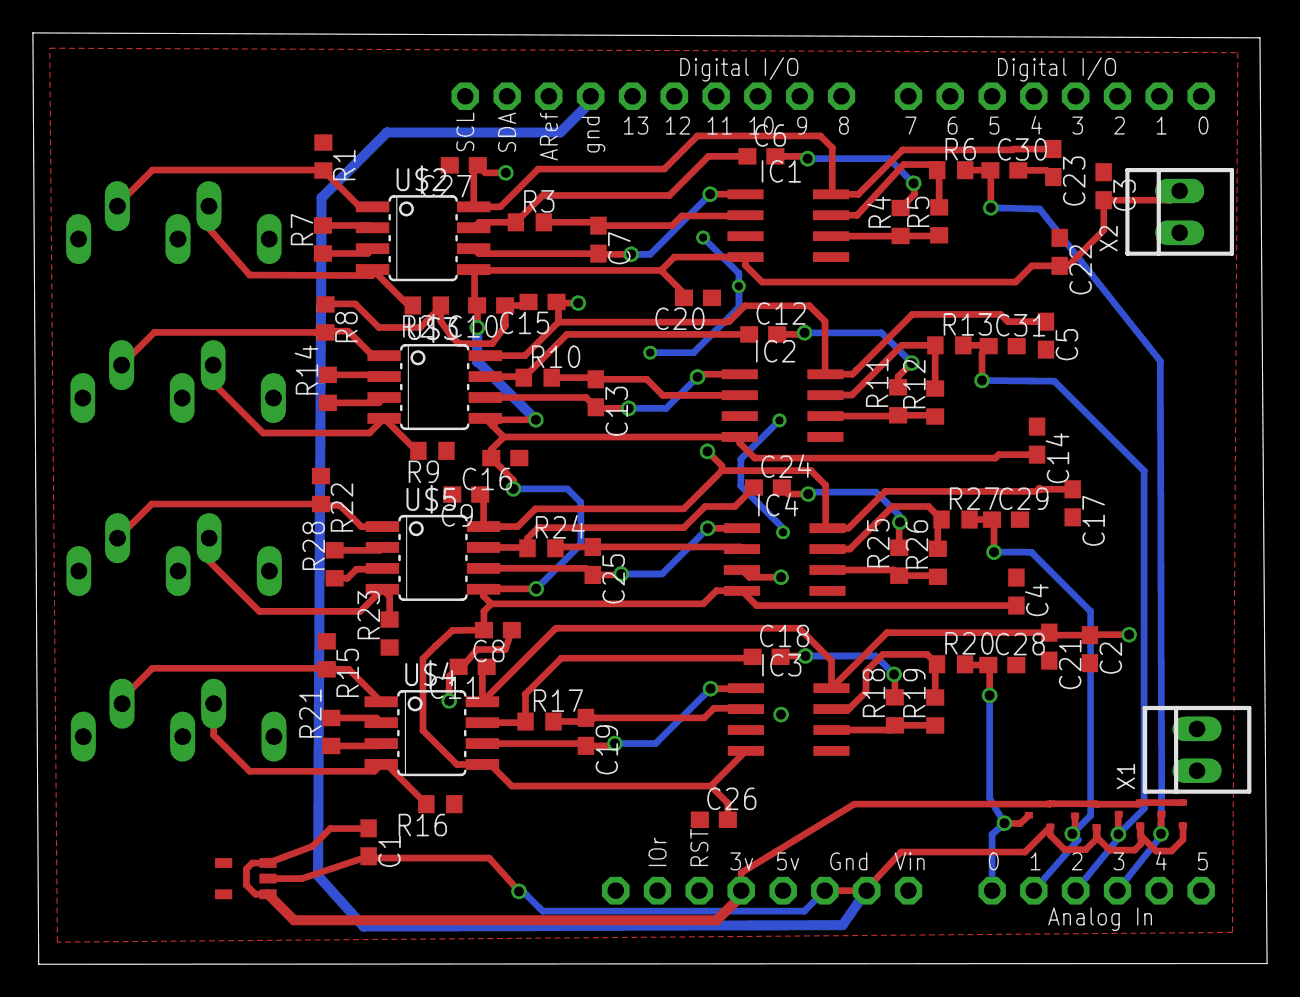
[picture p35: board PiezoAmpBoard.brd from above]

Board: 2 copper layers, 75.0 x 56.6 mm, 79 parts (0 on the bottom side), 49 nets.

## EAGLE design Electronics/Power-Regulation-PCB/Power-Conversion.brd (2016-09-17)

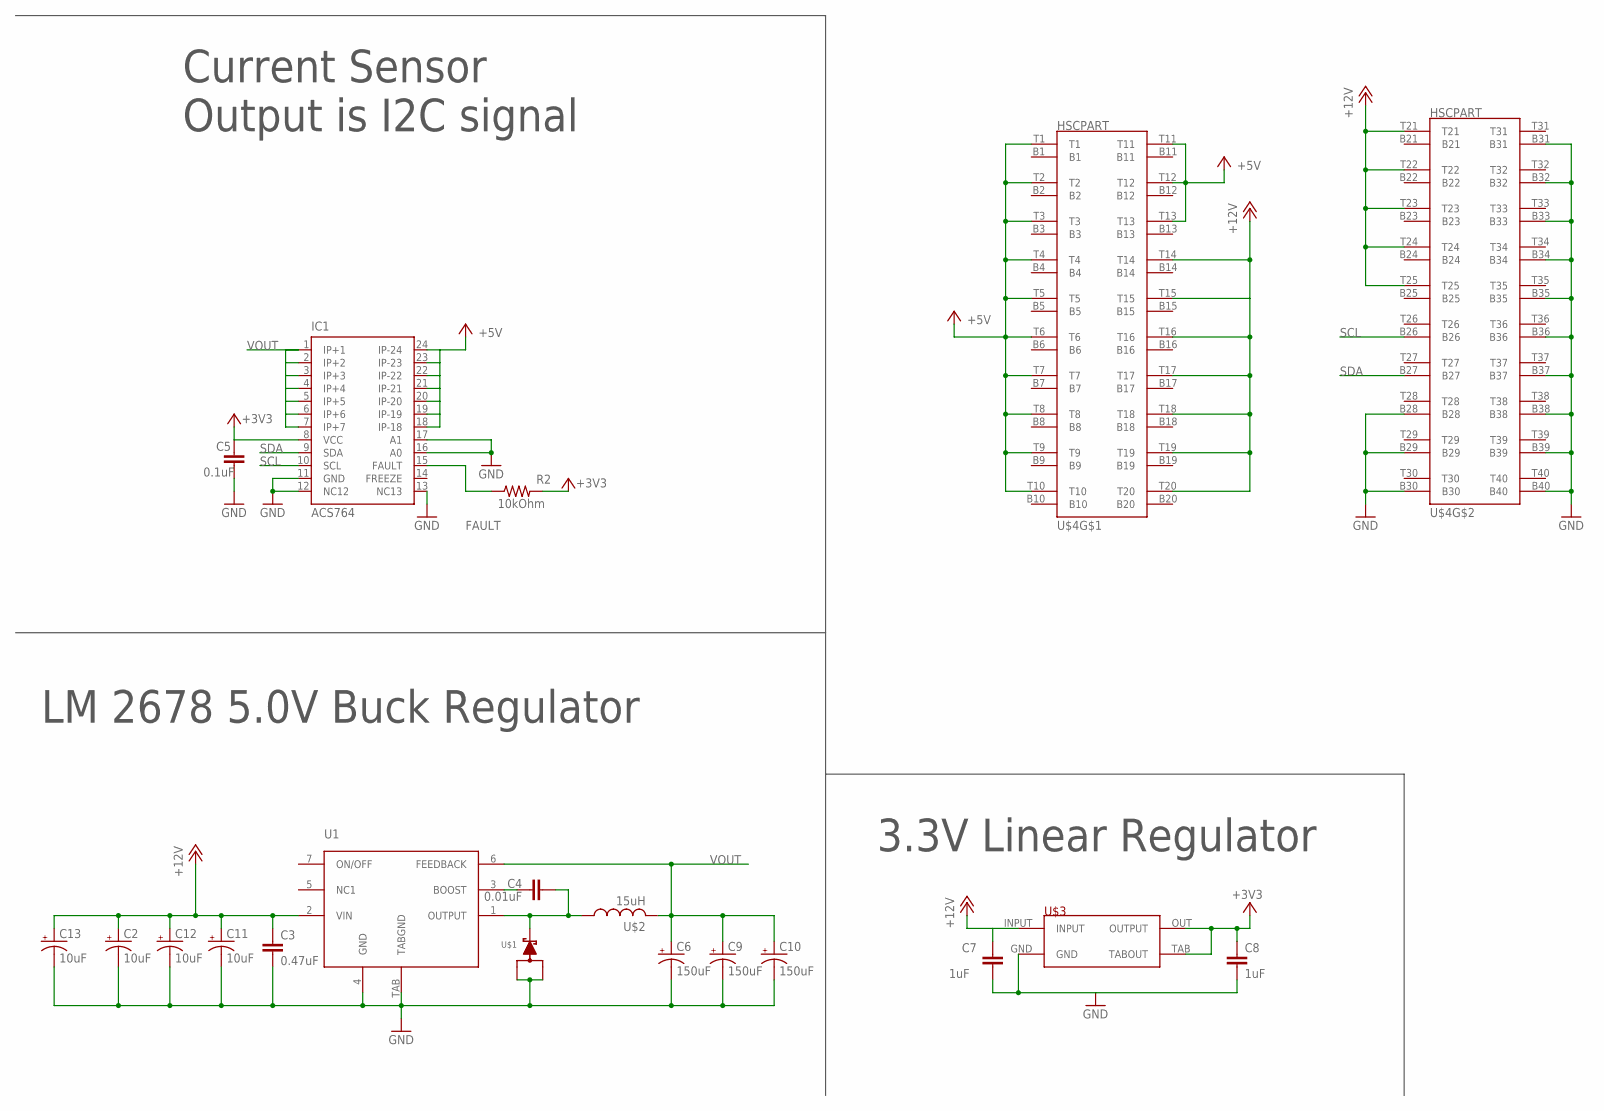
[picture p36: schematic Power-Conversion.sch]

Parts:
C2, C11, C12, C13: 10uF; CTAN(7.30_4.30MM)
C3: 0.47uF; 0805
C4: 0.01uF; 0603-CAP
C5: 0.1uF; C0603
C6, C9, C10: 150uF; CTAN(7.30_4.30MM)
C7, C8: 1uF; 0603-CAP
IC1: ACS764; SSOP24
R2: 10kOhm; R0603
U1: LM2678
U$1: SWITCHMODE_SCHOTTKY; DPAK-3
U$2: 15uH; HCMA1305
U$3: NCP1117
U$4: HSCPART; HSC8-40PINOUUT

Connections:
+3V3: C5.1, C8.1, IC1.8 (VCC), R2.2, U$3.OUT (OUTPUT), U$3.TAB (TABOUT)
+5V: IC1.18 (IP-18), IC1.19 (IP-19), IC1.20 (IP-20), IC1.21 (IP-21), IC1.22 (IP-22), IC1.23 (IP-23), IC1.24 (IP-24), U$4.T1, U$4.T2, U$4.T3, U$4.T4, U$4.T5, U$4.T6, U$4.T7, U$4.T8, U$4.T9, U$4.T10, U$4.T11, U$4.T12, U$4.T13
+12V: C2.+, C3.1, C7.1, C11.+, C12.+, C13.+, U1.2 (VIN), U$3.INPUT, U$4.T14, U$4.T15, U$4.T16, U$4.T17, U$4.T18, U$4.T19, U$4.T20, U$4.T21, U$4.T22, U$4.T23, U$4.T24, U$4.T25
FAULT: IC1.15 (FAULT), R2.1
GND: C2.-, C3.2, C5.2, C6.-, C7.2, C8.2, C9.-, C10.-, C11.-, C12.-, C13.-, IC1.11 (GND), IC1.12 (NC12), IC1.13 (NC13), IC1.16 (A0), IC1.17 (A1), U1.4 (GND), U1.TAB (TABGND), U$1.P$1, U$1.P$3, U$3.GND, U$4.B28, U$4.B29, U$4.B30, U$4.B31, U$4.B32, U$4.B33, U$4.B34, U$4.B35, U$4.B36, U$4.B37, U$4.B38, U$4.B39, U$4.B40
unnamed: C4.1, U1.3 (BOOST)
unnamed: C4.2, U1.1 (OUTPUT), U$1.P$4, U$2.P$1 (1)
SCL: IC1.10 (SCL), U$4.B26
SDA: IC1.9 (SDA), U$4.B27
VOUT: C6.+, C9.+, C10.+, IC1.1 (IP+1), IC1.2 (IP+2), IC1.3 (IP+3), IC1.4 (IP+4), IC1.5 (IP+5), IC1.6 (IP+6), IC1.7 (IP+7), U1.6 (FEEDBACK), U$2.P$2 (2)

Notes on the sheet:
LM 2678 5.0V Buck Regulator
3.3V Linear Regulator
Current Sensor Output is I2C signal

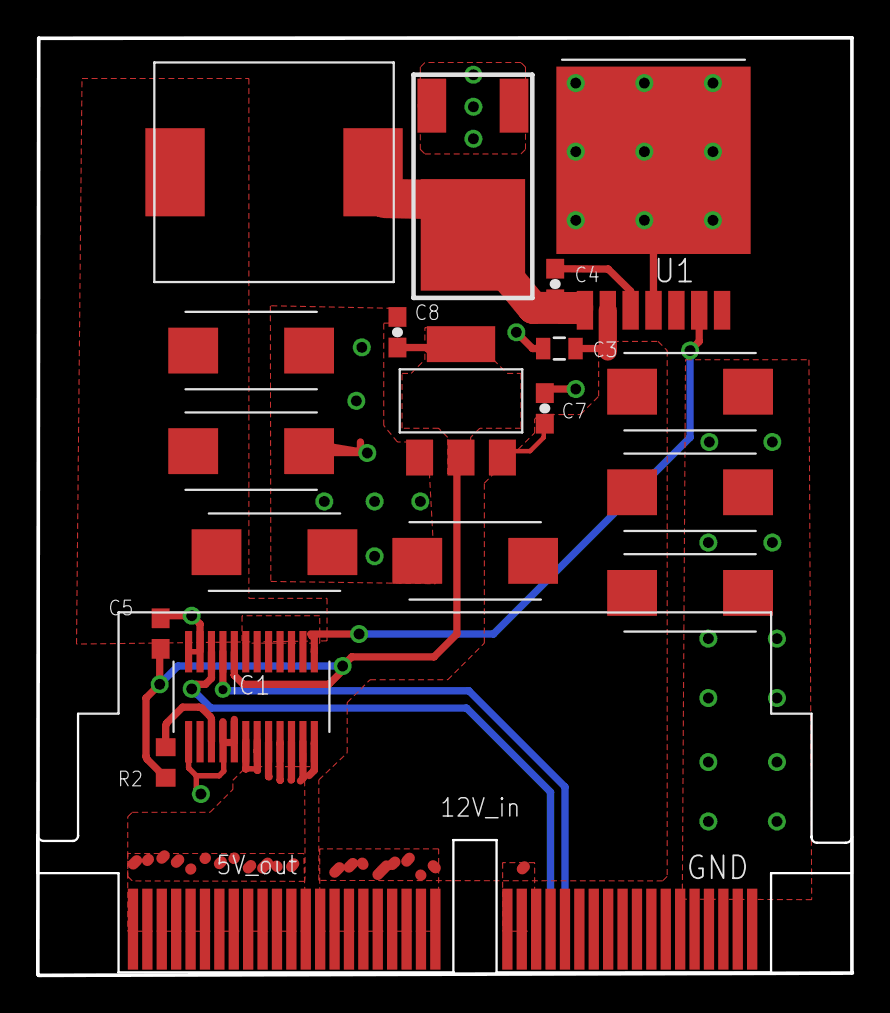
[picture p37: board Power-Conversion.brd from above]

Board: 2 copper layers, 45.3 x 52.1 mm, 19 parts (0 on the bottom side), 10 nets.

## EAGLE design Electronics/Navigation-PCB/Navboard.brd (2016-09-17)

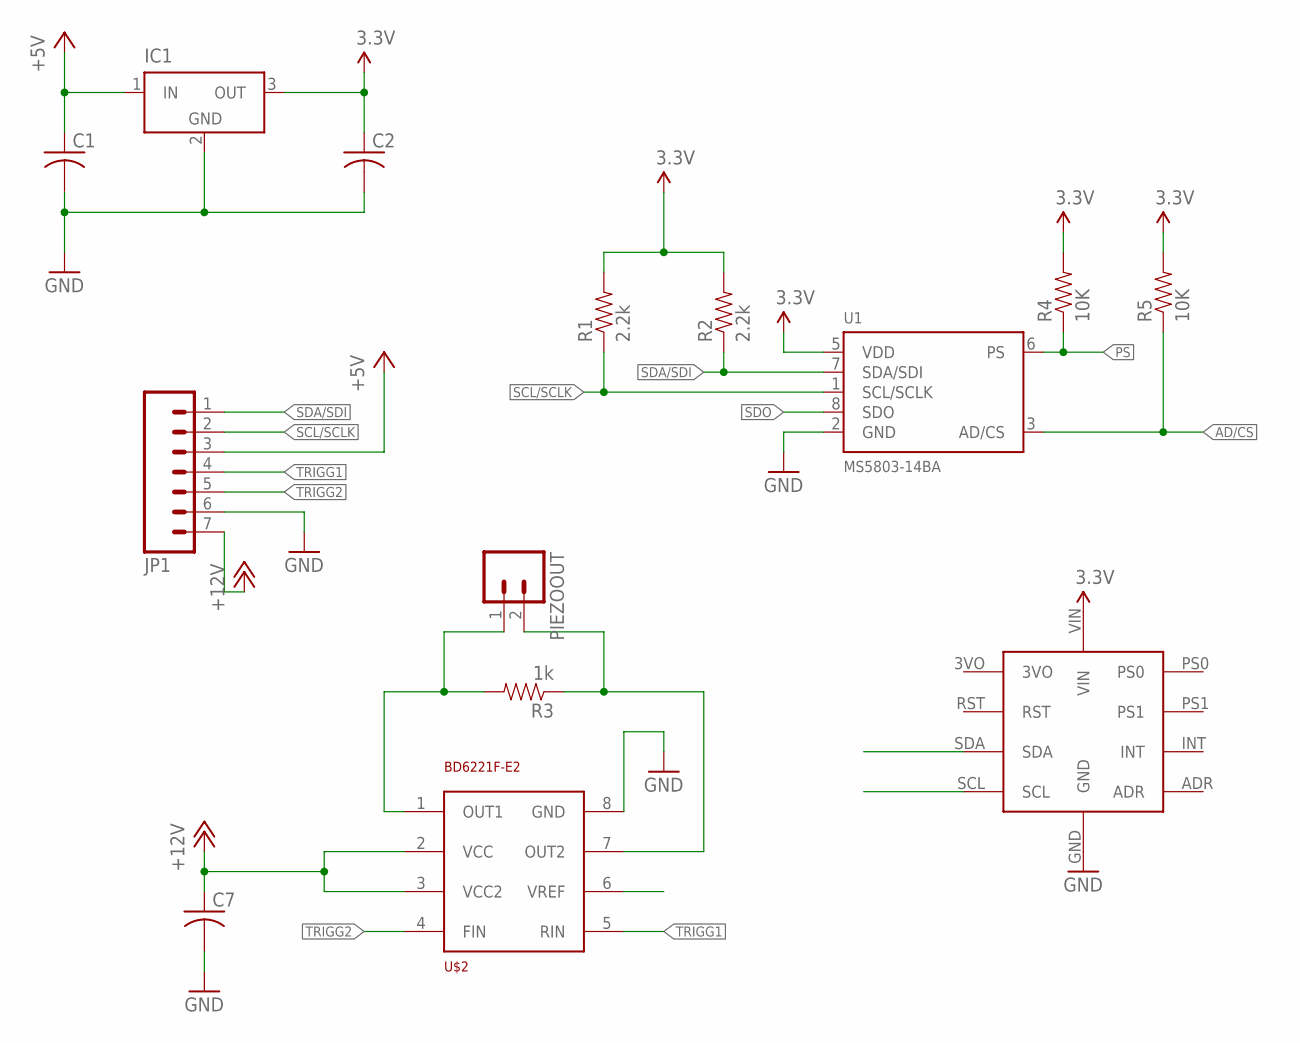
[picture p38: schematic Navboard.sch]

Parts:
C1, C2, C7: C-USC0603; C0603
IC1: LT1129CST5; SOT223
JP1: M07; 1X07
PIEZOOUT: M02LOCK_LONGPADS; 1X02_LOCK_LONGPADS
R1, R2: 2.2k; 0603-RES
R3: 1k; 0603-RES
R4, R5: 10K; 0603-RES
U1: MS5803-14BA; MS5803
U$1: BNO055_9DOF_BREAKOUT; BNO055
U$2: BD6221F-E2; SOIC8

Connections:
3.3V: C2.1, IC1.3 (OUT), R1.2, R2.2, R4.2, R5.2, U1.5 (VDD), U$1.VIN
+5V: C1.1, IC1.1 (IN), JP1.3
+12V: C7.1, JP1.7, U$2.2 (VCC), U$2.3 (VCC2)
AD/CS: R5.1, U1.3 (AD/CS)
GND: C1.2, C2.2, C7.2, IC1.2 (GND), IC1.4 (GND), JP1.6, U1.2 (GND), U$1.GND, U$2.8 (GND)
unnamed: PIEZOOUT.1, R3.2, U$2.1 (OUT1)
unnamed: PIEZOOUT.2, R3.1, U$2.7 (OUT2)
PS: R4.1, U1.6 (PS)
SCL/SCLK: JP1.2, R1.1, U1.1 (SCL/SCLK), U$1.SCL
SDA/SDI: JP1.1, R2.1, U1.7 (SDA/SDI), U$1.SDA
SDO: U1.8 (SDO)
TRIGG1: JP1.4, U$2.5 (RIN)
TRIGG2: JP1.5, U$2.4 (FIN)

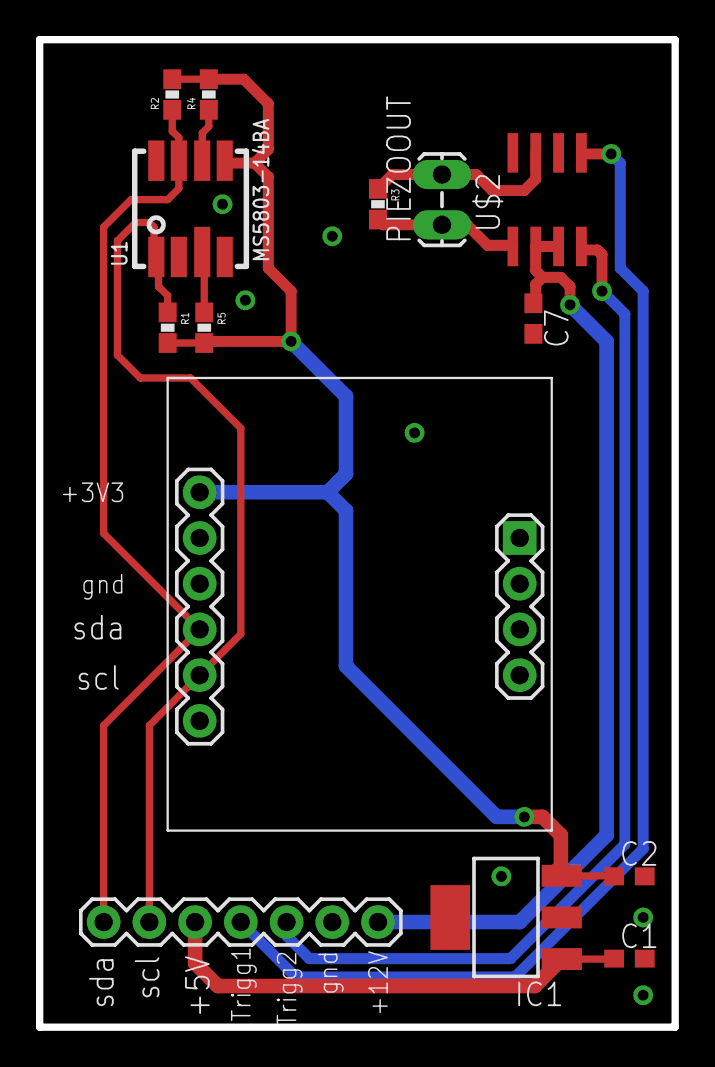
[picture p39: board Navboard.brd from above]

Board: 2 copper layers, 35.3 x 54.9 mm, 14 parts (0 on the bottom side), 12 nets.

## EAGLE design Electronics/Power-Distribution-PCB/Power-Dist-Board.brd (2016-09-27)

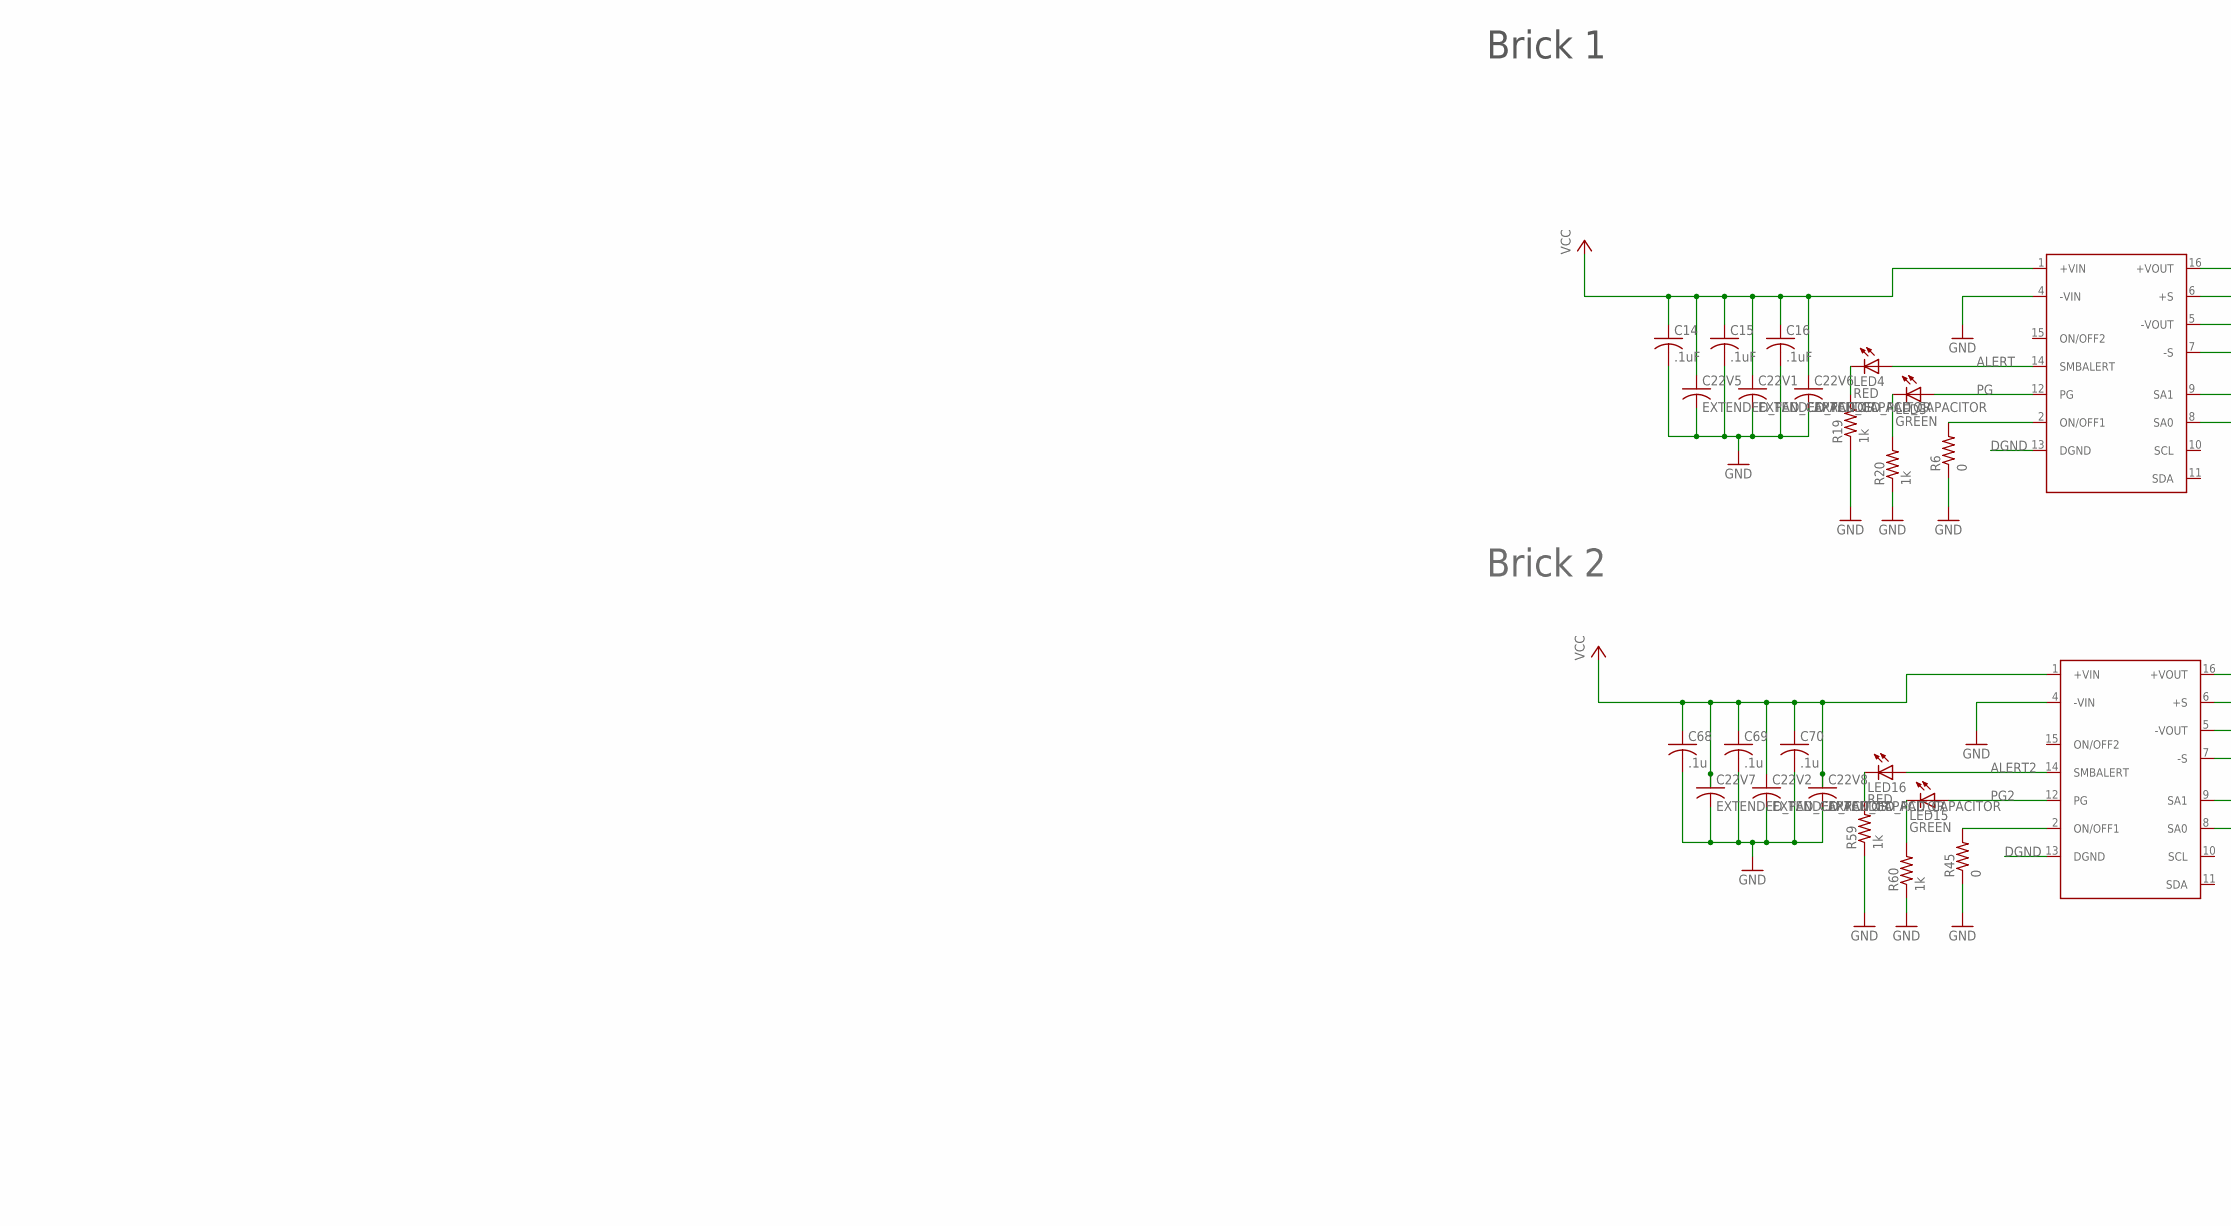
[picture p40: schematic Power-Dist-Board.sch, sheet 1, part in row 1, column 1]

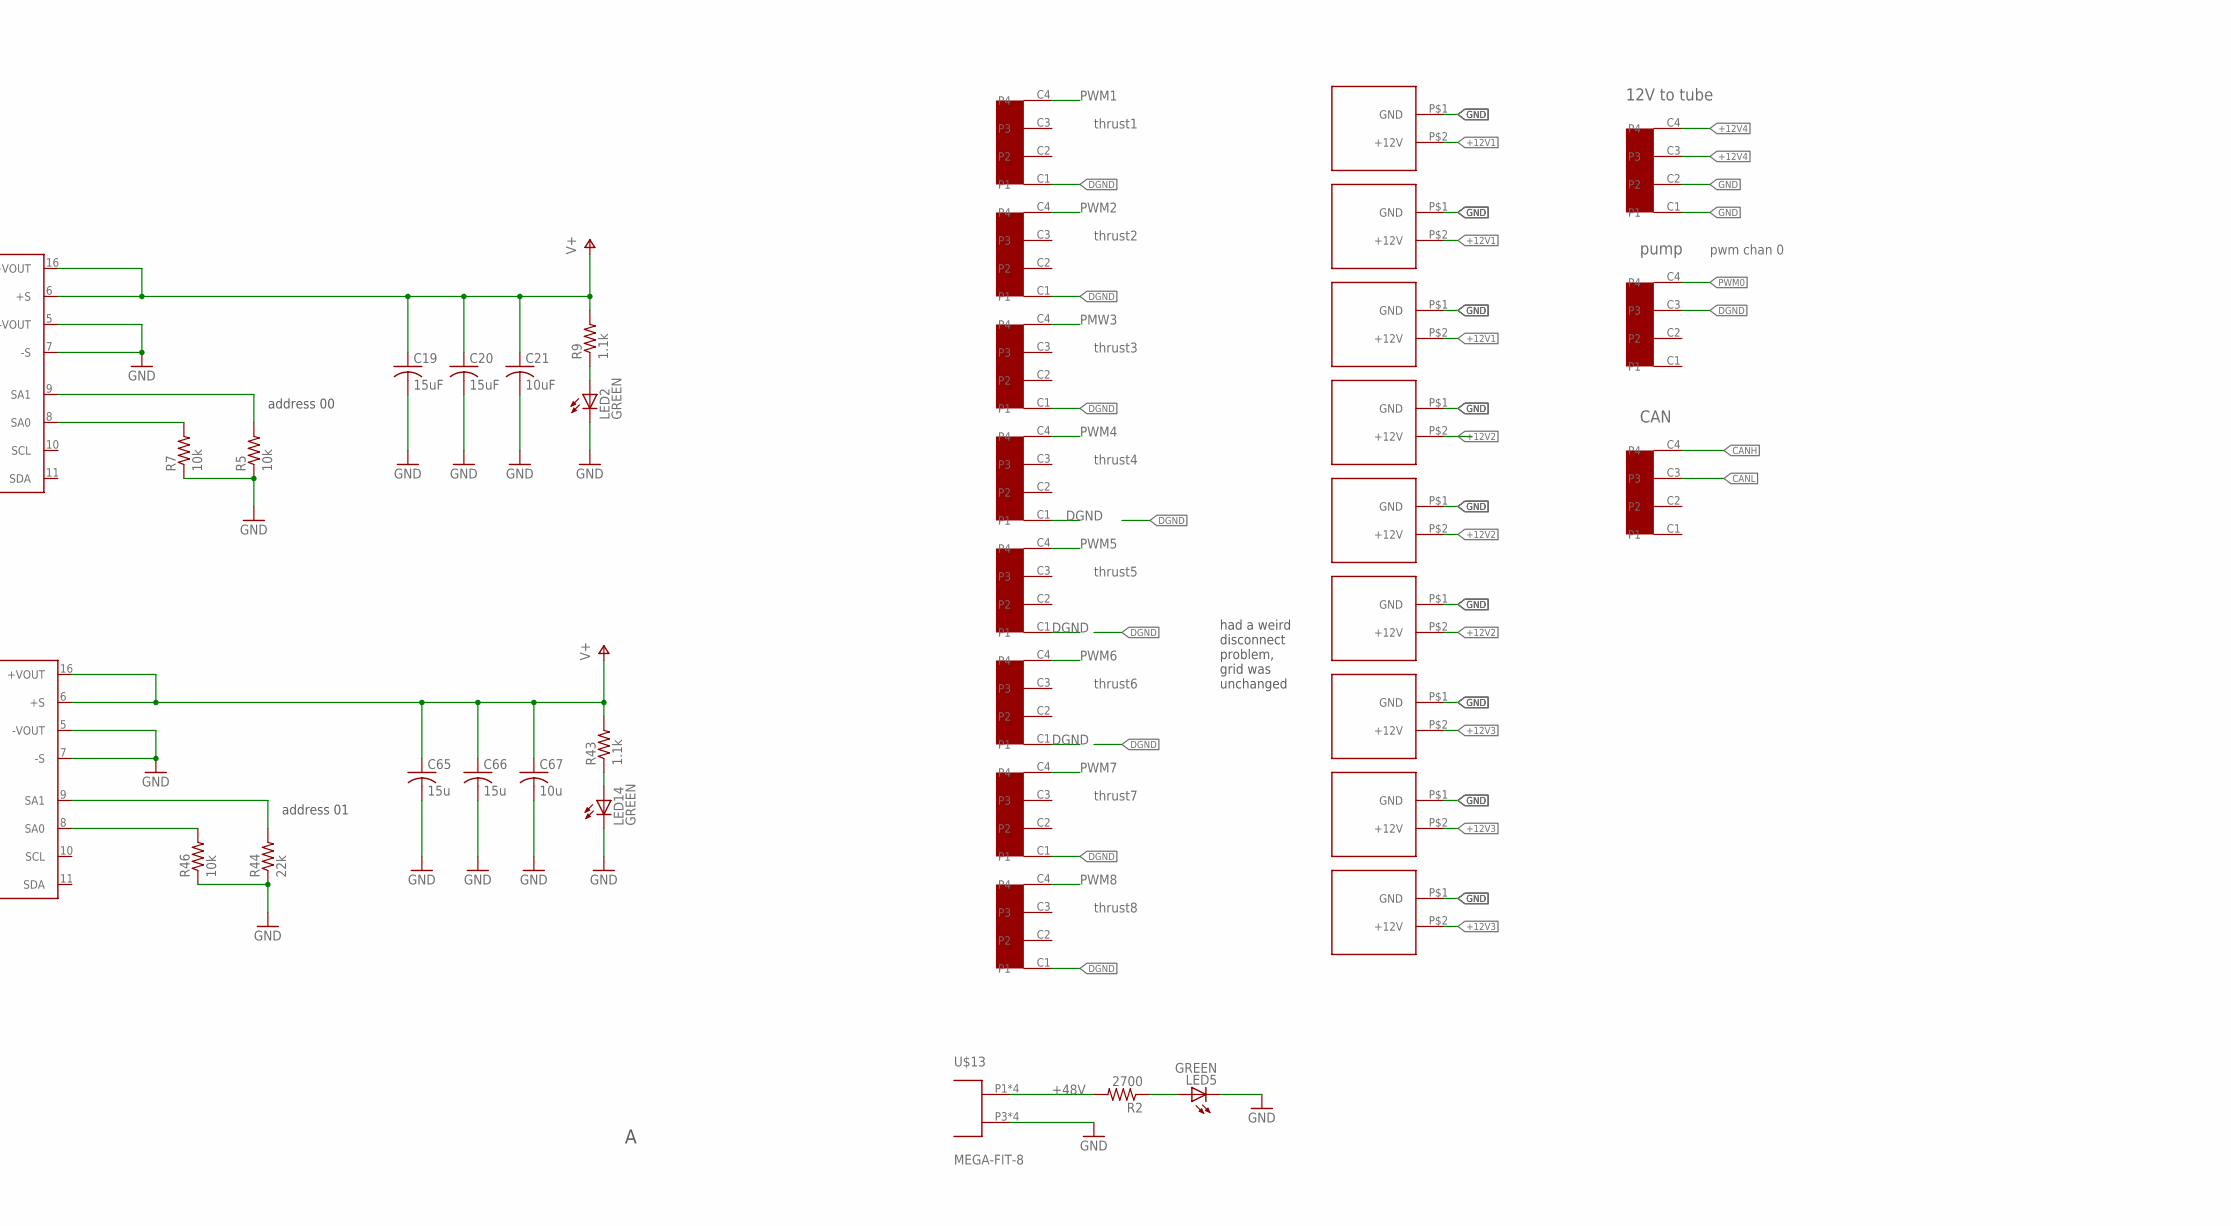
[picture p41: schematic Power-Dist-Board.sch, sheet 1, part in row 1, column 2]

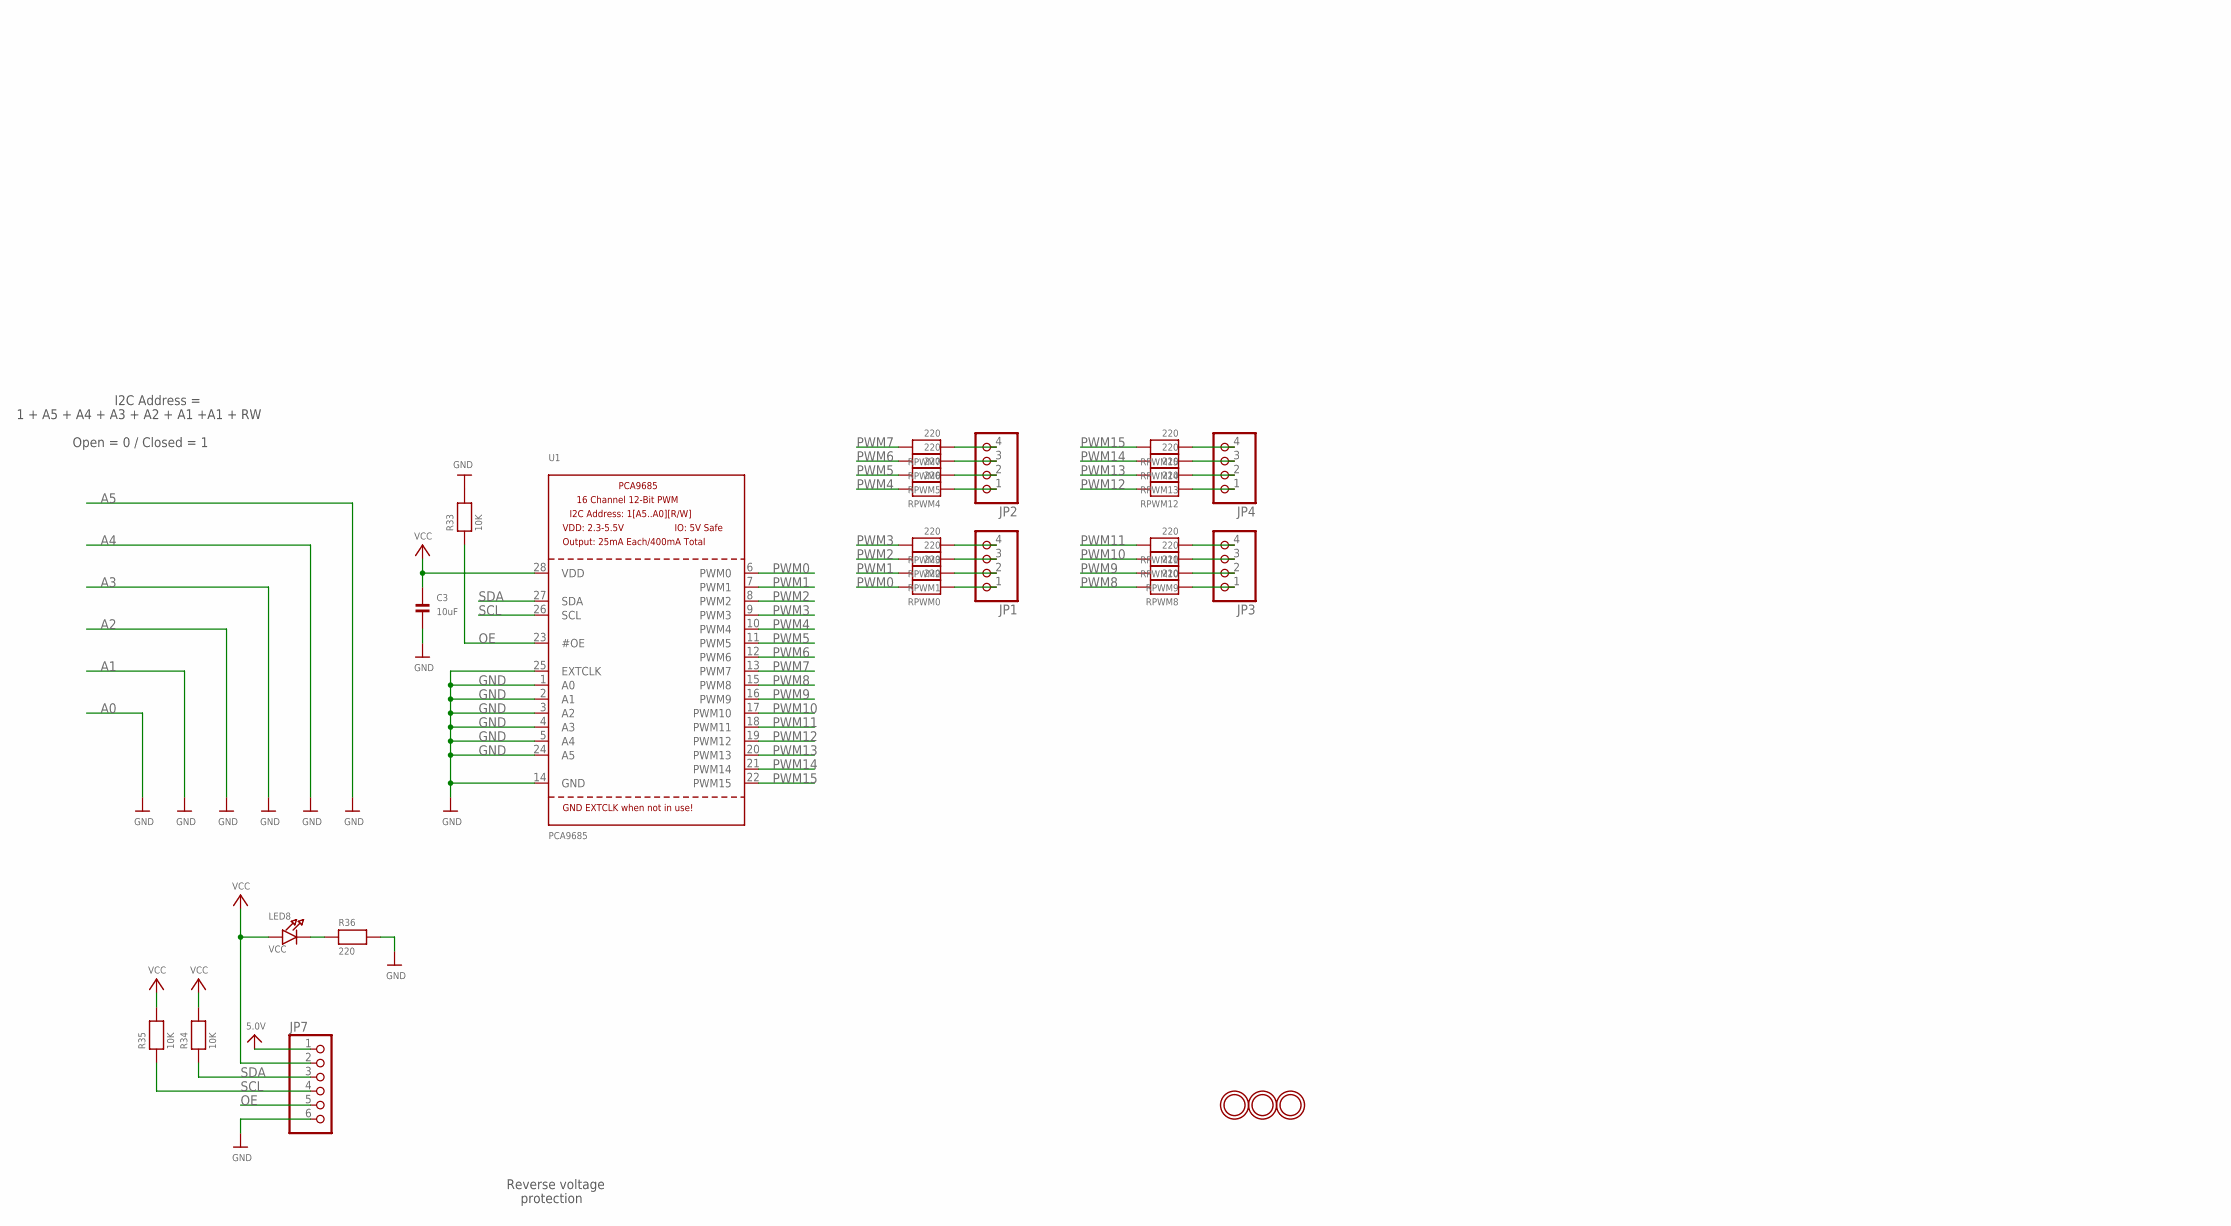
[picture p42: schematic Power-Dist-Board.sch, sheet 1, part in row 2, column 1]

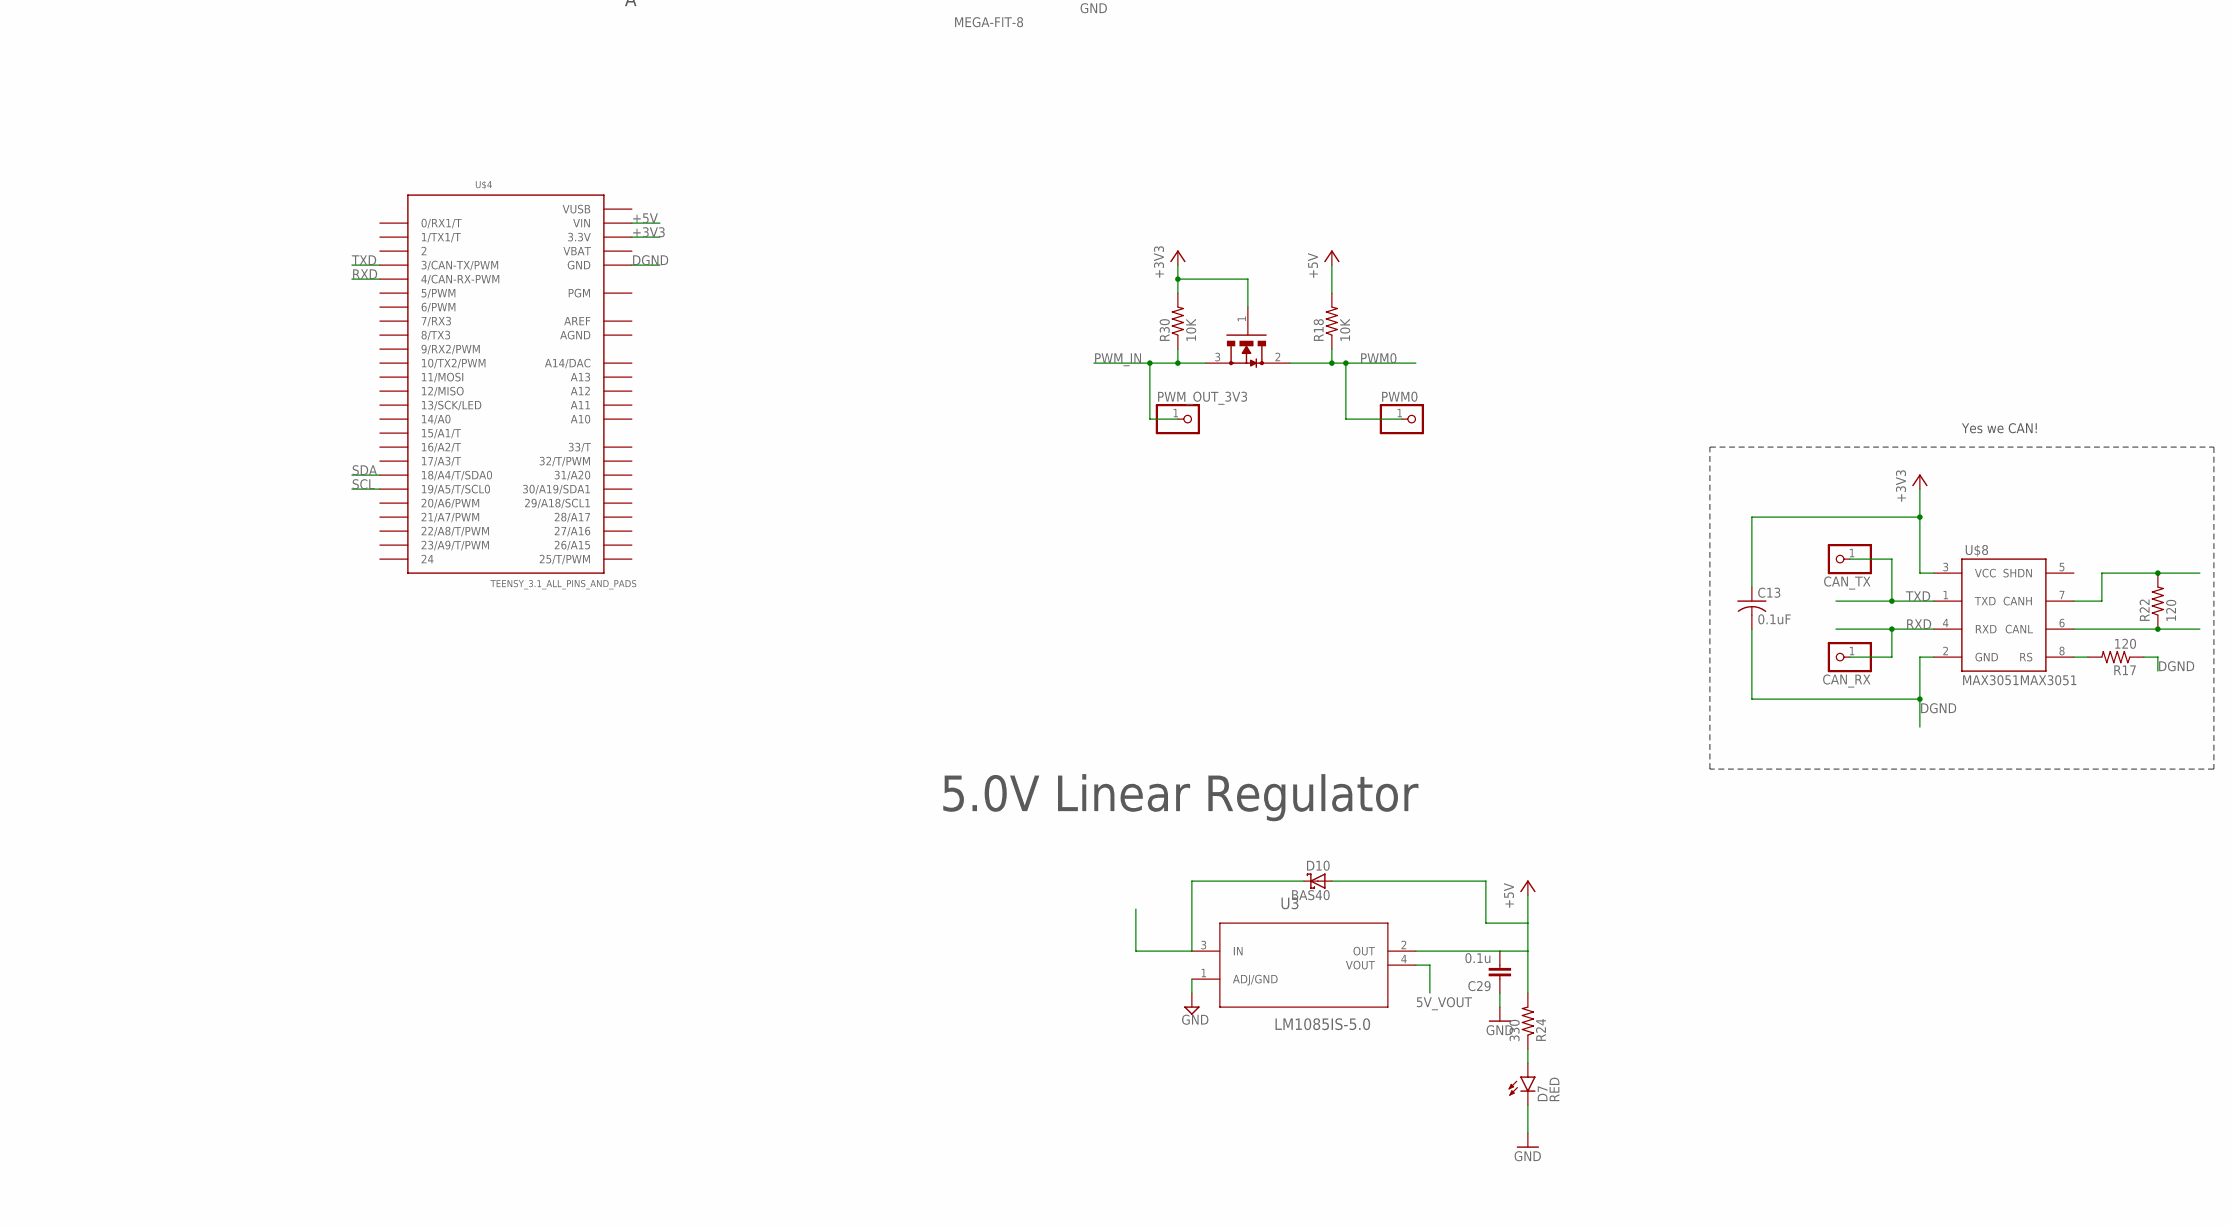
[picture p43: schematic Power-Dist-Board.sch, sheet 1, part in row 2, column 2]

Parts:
BRICK1, BRICK2: BRICK_DC-DC_CONVERTER
C3: 10uF; 0805
C13: 0.1uF; C0603
C14, C15, C16: .1uF; C0603
C19, C20: 15uF; C3216
C21: 10uF; C0603
C22V1, C22V2, C22V5, C22V6, C22V7, C22V8: EXTENDED_PAD_CAPACITOR; MODIFIED-NICHICON-UX-8X10
C29: 0.1u; C0603
C65, C66: 15u; C3216
C67: 10u; C0603
C68, C69, C70: .1u; C0603
CAN_RX: PINHD-1X1; 1X01
CAN_TX: PINHD-1X1; 1X01
D7: RED; LED-0603
D10: BAS40; SOT23
JP1, JP2, JP3, JP4: PINHD-1X4; 1X04
JP7: PINHD-1X6CB; 1X06-CLEANBIG
LED2, LED3, LED5, LED14, LED15: GREEN; LED-0603; PARTNO 160-1446-1-ND
LED4, LED16: RED; LED-0603; PARTNO 160-1446-1-ND
LED8: VCC; CHIPLED_0805
PWM0: PINHD-1X1; 1X01
PWM_OUT_3V3: PINHD-1X1; 1X01
R2: 2700; R2512; PARTNO RHC2512FT2K20CT-ND
R5, R7, R46: 10k; R0603; PARTNO 1.00MHCT-ND
R6, R45: 0; R0603; PARTNO 1.00MHCT-ND
R9, R43: 1.1k; R1206; PARTNO RNCP1206FTD1K10CT-ND
R17, R22: 120; R0603
R18, R30: 10K; R0603
R19, R20, R59, R60: 1k; R0603; PARTNO 1.00MHCT-ND
R24: 330; R0603
R33, R34, R35: 10K; 0805
R36: 220; 0805
R44: 22k; R0603; PARTNO 1.00MHCT-ND
RPWM0, RPWM1, RPWM2, RPWM3, RPWM4, RPWM5, RPWM6, RPWM7, RPWM8, RPWM9, RPWM10, RPWM11, RPWM12, RPWM13, RPWM14, RPWM15: 220; 0805
U1: PCA9685; TSSOP28
U3: LM1085IS-5.0; TO254P1435X457-3N
U$2, U$3, U$10, U$11, U$16, U$17, U$18, U$19, U$21: XT60
U$4: TEENSY_3.1_ALL_PINS_AND_PADS; TEENSY3_ALL_PINS_&_PADS
U$8: MAX3051MAX3051; SOT23-8L
U$12: BSS138; SOT-23-BSS138
U$13: MEGA-FIT-8
U$100, U$101, U$102: MOUNTINGHOLE2.5; MOUNTINGHOLE_2.5_PLATED
UFIT0, UFIT1, UFIT2, UFIT3, UFIT4, UFIT5, UFIT6, UFIT7, UFIT8: MICRO-FIT-4-SMD-HZVT; MICRO-FIT-4-SMD(CORRECTED)
UFITCAN: MICRO-FIT-4-SMD-HZVT; MICRO-FIT-4-SMD(CORRECTED)
UFITTUBE: MICRO-FIT-4-SMD-HZVT; MICRO-FIT-4-SMD(CORRECTED)

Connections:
5V_VOUT: U3.4 (VOUT)
+3V3: C13.1, R30.2, U$4.3.3V, U$4.3.3V1 (3.3V), U$4.3.3V2 (3.3V), U$8.3 (VCC), U$12.1 (G)
+5V: C3.1, C29.2, D10.1 (A), JP7.1, JP7.2, LED8.A, R18.2, R24.2, R34.2, R35.2, U1.28 (VDD), U3.2 (OUT), U$4.VIN
+12V1: BRICK1.6 (+S), BRICK1.16 (+VOUT), C19.1, C20.1, C21.1, R9.2, U$2.P$2 (+12V), U$3.P$2 (+12V), U$10.P$2 (+12V)
+12V2: BRICK2.6 (+S), BRICK2.16 (+VOUT), C65.1, C66.1, C67.1, R43.2, U$11.P$2 (+12V), U$16.P$2 (+12V), U$17.P$2 (+12V)
+12V3: U$18.P$2 (+12V), U$19.P$2 (+12V), U$21.P$2 (+12V); also elsewhere on the board
+12V4: D10.3 (C), U3.3 (IN), UFITTUBE.C3 (P3), UFITTUBE.C4 (P4); also elsewhere on the board
+48V: BRICK1.1 (+VIN), BRICK2.1 (+VIN), C14.1, C15.1, C16.1, C22V1.P$3 (3), C22V2.P$3 (3), C22V5.P$3 (3), C22V6.P$3 (3), C22V7.P$3 (3), C22V8.P$3 (3), C68.1, C69.1, C70.1, R2.2, U$13.P1, U$13.P2, U$13.P5, U$13.P6; also elsewhere on the board
ADRS00A: BRICK1.8 (SA0), R7.2
ADRS00A4: BRICK2.8 (SA0), R46.2
ADRS00B: BRICK1.9 (SA1), R5.2
ADRS00B4: BRICK2.9 (SA1), R44.2
AGND: U$4.AGND
ALERT: BRICK1.14 (SMBALERT), LED4.A
ALERT2: BRICK2.14 (SMBALERT), LED16.A
AREF: U$4.AREF
CANH: R22.2, U$8.7 (CANH), UFITCAN.C4 (P4)
CANL: R22.1, U$8.6 (CANL), UFITCAN.C3 (P3)
DGND: BRICK1.13 (DGND), BRICK2.13 (DGND), C13.2, R17.1, U$4.GND, U$4.GND1 (GND), U$4.GND2 (GND), U$8.2 (GND), UFIT0.C1 (P1), UFIT1.C1 (P1), UFIT2.C3 (P3), UFIT3.C1 (P1), UFIT4.C1 (P1), UFIT5.C1 (P1), UFIT6.C1 (P1), UFIT7.C1 (P1), UFIT8.C1 (P1); also elsewhere on the board
GND: BRICK1.4 (-VIN), BRICK1.5 (-VOUT), BRICK1.7 (-S), BRICK2.4 (-VIN), BRICK2.5 (-VOUT), BRICK2.7 (-S), C3.2, C14.2, C15.2, C16.2, C19.2, C20.2, C21.2, C22V1.P$1 (4), C22V2.P$1 (4), C22V5.P$1 (4), C22V6.P$1 (4), C22V7.P$1 (4), C22V8.P$1 (4), C29.1, C65.2, C66.2, C67.2, C68.2, C69.2, C70.2, D7.C, JP7.6, LED2.C, LED5.C, LED14.C, R5.1, R6.1, R7.1, R19.1, R20.1, R33.2, R36.2, R44.1, R45.1, R46.1, R59.1, R60.1, U1.1 (A0), U1.2 (A1), U1.3 (A2), U1.4 (A3), U1.5 (A4), U1.14 (GND), U1.24 (A5), U1.25 (EXTCLK), U3.1 (ADJ/GND), U$2.P$1 (GND), U$3.P$1 (GND), U$10.P$1 (GND), U$11.P$1 (GND), U$13.P3, U$13.P4, U$13.P7, U$13.P8, U$16.P$1 (GND), U$17.P$1 (GND), U$18.P$1 (GND), U$19.P$1 (GND), U$21.P$1 (GND), UFITTUBE.C1 (P1), UFITTUBE.C2 (P2); also elsewhere on the board
unnamed: BRICK1.2 (ON/OFF1), R6.2
unnamed: LED5.A, R2.1
unnamed: LED4.C, R19.2
unnamed: LED3.C, R20.2
unnamed: LED2.A, R9.1
unnamed: LED8.C, R36.1
unnamed: JP2.3, RPWM6.1
unnamed: JP2.4, RPWM7.1
unnamed: JP2.2, RPWM5.1
unnamed: D7.A, R24.1
unnamed: LED14.A, R43.1
unnamed: JP2.1, RPWM4.1
unnamed: BRICK2.2 (ON/OFF1), R45.2
unnamed: JP1.4, RPWM3.1
unnamed: JP1.3, RPWM2.1
unnamed: JP1.2, RPWM1.1
unnamed: JP1.1, RPWM0.1
unnamed: JP3.1, RPWM8.1
unnamed: JP3.2, RPWM9.1
unnamed: JP3.3, RPWM10.1
unnamed: LED16.C, R59.2
unnamed: LED15.C, R60.2
unnamed: JP3.4, RPWM11.1
unnamed: JP4.1, RPWM12.1
unnamed: JP4.2, RPWM13.1
unnamed: JP4.3, RPWM14.1
unnamed: JP4.4, RPWM15.1
unnamed: R17.2, U$8.8 (RS)
OE: JP7.5, R33.1, U1.23 (#OE)
PG: BRICK1.12 (PG), LED3.A
PG2: BRICK2.12 (PG), LED15.A
PMW3: UFIT3.C4 (P4)
PWM0: PWM0.1, R18.1, RPWM0.2, U1.6 (PWM0), U$12.2 (D), UFIT2.C4 (P4)
PWM1: RPWM1.2, U1.7 (PWM1), UFIT1.C4 (P4)
PWM2: RPWM2.2, U1.8 (PWM2), UFIT0.C4 (P4)
PWM3: RPWM3.2, U1.9 (PWM3)
PWM4: RPWM4.2, U1.10 (PWM4), UFIT4.C4 (P4)
PWM5: RPWM5.2, U1.11 (PWM5), UFIT5.C4 (P4)
PWM6: RPWM6.2, U1.12 (PWM6), UFIT6.C4 (P4)
PWM7: RPWM7.2, U1.13 (PWM7), UFIT7.C4 (P4)
PWM8: RPWM8.2, U1.15 (PWM8), UFIT8.C4 (P4)
PWM9: RPWM9.2, U1.16 (PWM9)
PWM10: RPWM10.2, U1.17 (PWM10)
PWM11: RPWM11.2, U1.18 (PWM11)
PWM12: RPWM12.2, U1.19 (PWM12)
PWM13: RPWM13.2, U1.20 (PWM13)
PWM14: RPWM14.2, U1.21 (PWM14)
PWM15: RPWM15.2, U1.22 (PWM15)
PWM_IN: PWM_OUT_3V3.1, R30.1, U$12.3 (S)
RXD: CAN_RX.1, U$4.4 (4/CAN-RX-PWM), U$8.4 (RXD)
SCL: JP7.4, R35.1, U1.26 (SCL), U$4.19/A5 (19/A5/T/SCL0)
SDA: JP7.3, R34.1, U1.27 (SDA), U$4.18/A4 (18/A4/T/SDA0)
TXD: CAN_TX.1, U$4.3 (3/CAN-TX/PWM), U$8.1 (TXD)
VBAT: U$4.VBAT
VUSB: U$4.VUSB

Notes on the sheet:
address 00
Yes we CAN!
Brick 1
5.0V Linear Regulator
Brick 2
address 01
12V to tube
pump
CAN
Reverse voltage
protection
1 + A5 + A4 + A3 + A2 + A1 +A1 + RW
I2C Address =
Open = 0 / Closed = 1
thrust2
thrust1
thrust3
thrust4
thrust5
thrust6
thrust7
thrust8
pwm chan 0
had a weird disconnect problem, grid was unchanged

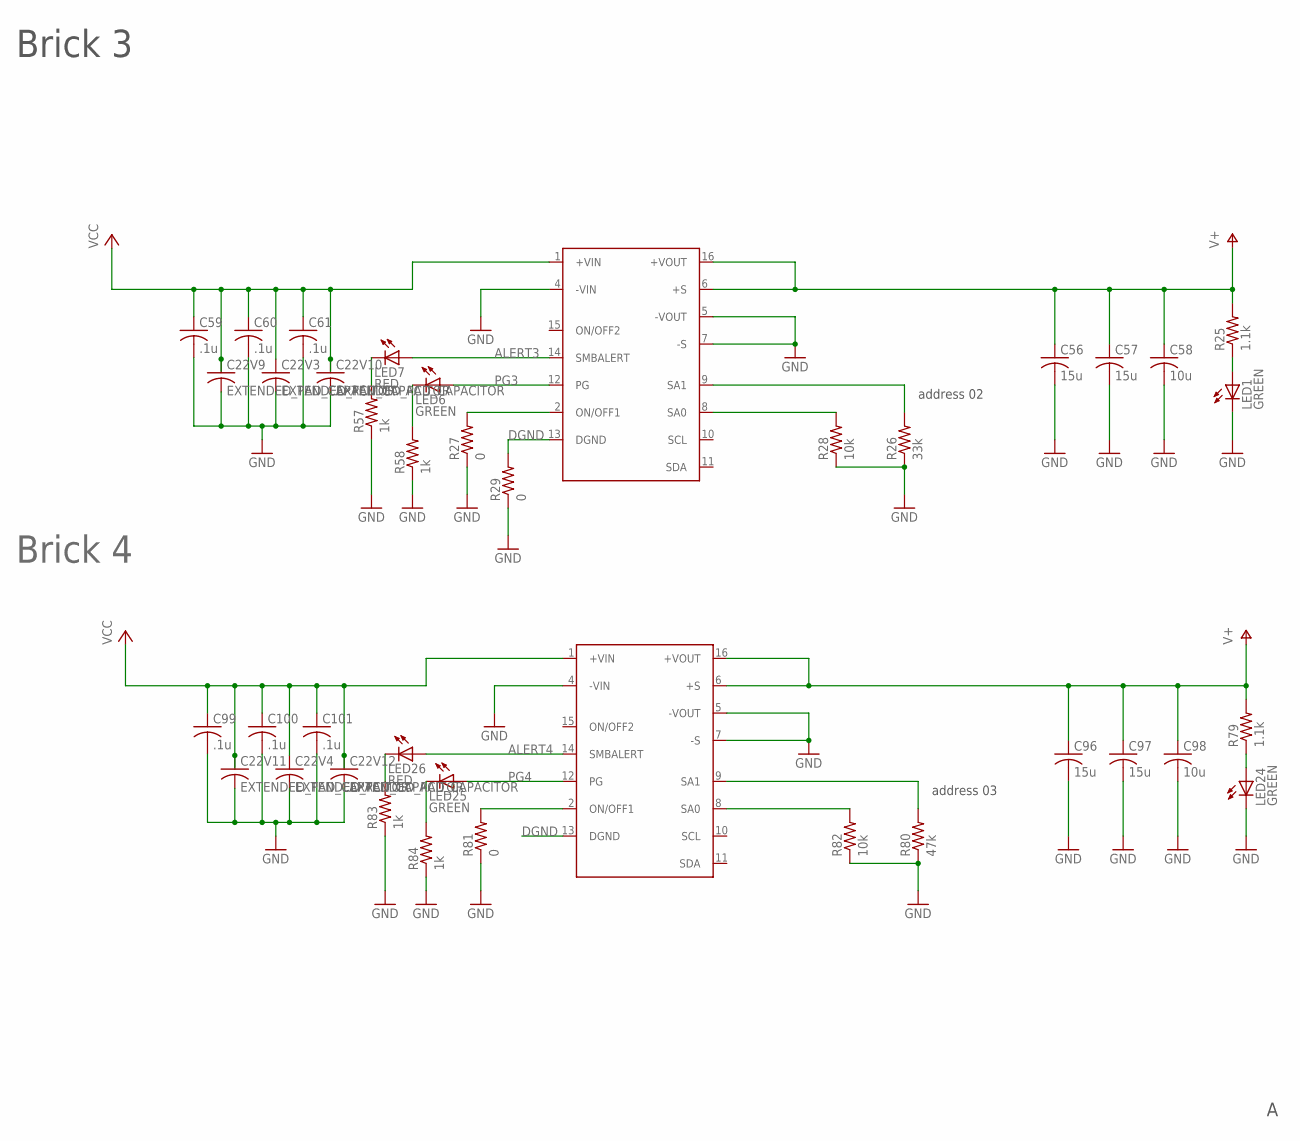
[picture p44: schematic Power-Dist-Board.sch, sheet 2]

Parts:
BRICK3, BRICK4: BRICK_DC-DC_CONVERTER
C22V3, C22V4, C22V9, C22V10, C22V11, C22V12: EXTENDED_PAD_CAPACITOR; MODIFIED-NICHICON-UX-8X10
C56, C57, C96, C97: 15u; C3216
C58, C98: 10u; C0603
C59, C60, C61, C99, C100, C101: .1u; C0603
LED1, LED6, LED24, LED25: GREEN; LED-0603; PARTNO 160-1446-1-ND
LED7, LED26: RED; LED-0603; PARTNO 160-1446-1-ND
R25, R79: 1.1k; R1206; PARTNO RNCP1206FTD1K10CT-ND
R26: 33k; R0603; PARTNO 1.00MHCT-ND
R27, R29, R81: 0; R0603; PARTNO 1.00MHCT-ND
R28, R82: 10k; R0603; PARTNO 1.00MHCT-ND
R57, R58, R83, R84: 1k; R0603; PARTNO 1.00MHCT-ND
R80: 47k; R0603; PARTNO 1.00MHCT-ND

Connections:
+12V3: BRICK3.6 (+S), BRICK3.16 (+VOUT), C56.1, C57.1, C58.1, R25.2; also elsewhere on the board
+12V4: BRICK4.6 (+S), BRICK4.16 (+VOUT), C96.1, C97.1, C98.1, R79.2; also elsewhere on the board
+48V: BRICK3.1 (+VIN), BRICK4.1 (+VIN), C22V3.P$3 (3), C22V4.P$3 (3), C22V9.P$3 (3), C22V10.P$3 (3), C22V11.P$3 (3), C22V12.P$3 (3), C59.1, C60.1, C61.1, C99.1, C100.1, C101.1; also elsewhere on the board
ADRS00A1: BRICK3.8 (SA0), R28.2
ADRS00A5: BRICK4.8 (SA0), R82.2
ADRS00B1: BRICK3.9 (SA1), R26.2
ADRS00B5: BRICK4.9 (SA1), R80.2
ALERT3: BRICK3.14 (SMBALERT), LED7.A
ALERT4: BRICK4.14 (SMBALERT), LED26.A
DGND: BRICK3.13 (DGND), BRICK4.13 (DGND), R29.2; also elsewhere on the board
GND: BRICK3.4 (-VIN), BRICK3.5 (-VOUT), BRICK3.7 (-S), BRICK4.4 (-VIN), BRICK4.5 (-VOUT), BRICK4.7 (-S), C22V3.P$1 (4), C22V4.P$1 (4), C22V9.P$1 (4), C22V10.P$1 (4), C22V11.P$1 (4), C22V12.P$1 (4), C56.2, C57.2, C58.2, C59.2, C60.2, C61.2, C96.2, C97.2, C98.2, C99.2, C100.2, C101.2, LED1.C, LED24.C, R26.1, R27.1, R28.1, R29.1, R57.1, R58.1, R80.1, R81.1, R82.1, R83.1, R84.1; also elsewhere on the board
unnamed: LED1.A, R25.1
unnamed: BRICK3.2 (ON/OFF1), R27.2
unnamed: LED7.C, R57.2
unnamed: LED6.C, R58.2
unnamed: LED24.A, R79.1
unnamed: BRICK4.2 (ON/OFF1), R81.2
unnamed: LED26.C, R83.2
unnamed: LED25.C, R84.2
PG3: BRICK3.12 (PG), LED6.A
PG4: BRICK4.12 (PG), LED25.A

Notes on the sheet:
address 02
Brick 3
Brick 4
address 03

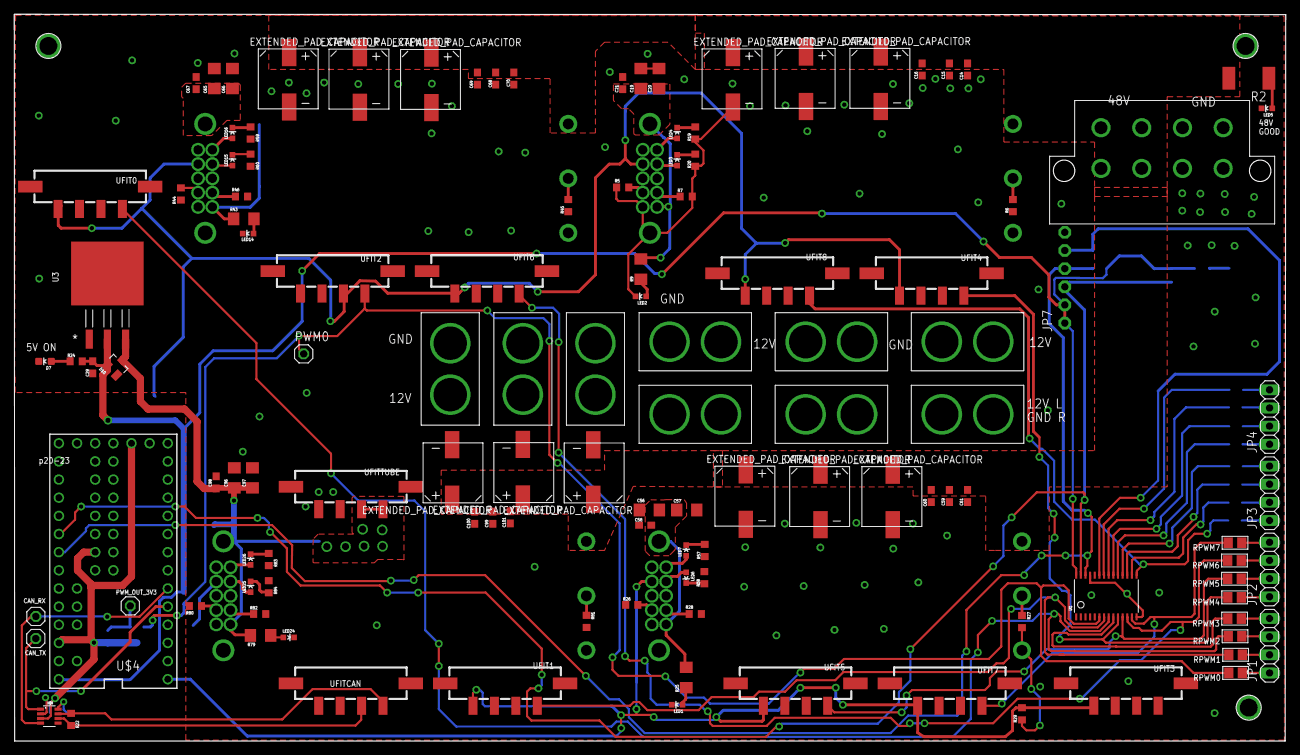
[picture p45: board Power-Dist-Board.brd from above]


Board: 2 copper layers, 177.9 x 101.7 mm, 148 parts (23 on the bottom side), 85 nets.

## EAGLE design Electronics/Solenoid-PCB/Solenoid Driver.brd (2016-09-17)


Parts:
1, 2, 3, 4, 5, 6, 7, 8, 9, 10, 11, 12, 13, 14, 15, 16: SE14
C1: 0.1uF; 0603-CAP
C2: 10uF; 0603-CAP
JP1, JP2, JP3, JP4: STAND-OFF
LED1: Orange; LED-0603
R1: 330; 0603-RES
U1: TPIC6A596; SOIC20-W
X1, X2: 87758-0816

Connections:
5V: C1.1, C2.1, U1.2 (VCC), U1.8 (SRCLR), X2.5
CLOCK: U1.12 (RCK), U1.13 (SRCK), X2.2
ENABLE: U1.9 (G), X2.4
GND: C1.2, C2.2, LED1.C, U1.10 (GND), U1.11 (GND), U1.19 (GND), X1.5, X1.6, X1.7, X1.8, X2.1, X2.3
unnamed: LED1.A, R1.2
SER-IN: U1.3 (SERIAL-IN), X2.6
SER-OUT: R1.1, U1.18 (SERIAL-OUT)
SOL-1A: 1.MP, U1.4 (DRAIN0)
SOL-1B: 2.MP, U1.5 (DRAIN1)
SOL-2A: 3.MP, U1.6 (DRAIN2)
SOL-2B: 4.MP, U1.7 (DRAIN3)
SOL-3A: 5.MP, U1.14 (DRAIN4)
SOL-3B: 6.MP, U1.15 (DRAIN5)
SOL-4A: 7.MP, U1.16 (DRAIN6)
SOL-4B: 8.MP, U1.17 (DRAIN7)
VCC: 9.MP, 10.MP, 11.MP, 12.MP, 13.MP, 14.MP, 15.MP, 16.MP, X1.1, X1.2, X1.3, X1.4

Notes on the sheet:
TPIC6B595


Board: 2 copper layers, 34.2 x 31.0 mm, 27 parts (0 on the bottom side), 16 nets.

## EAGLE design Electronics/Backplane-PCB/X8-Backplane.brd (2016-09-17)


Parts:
APPLICATION_BOARD: HSEC8-140-01-XX-DV-A
BRICKS_COM: MICRO-FIT-4-SMD-PART; MICRO-FIT-4-SMD
BUCK_REGULATOR_BOARD: HSEC8-140-01-XX-DV-A
ETH_POWER: MICRO-FIT-4-SMD-PART; MICRO-FIT-4-SMD
EXTRA_SERVO: MICRO-FIT-4-SMD-PART; MICRO-FIT-4-SMD
MAIN_CAM_DATA: MICRO-FIT-4-SMD-PART; MICRO-FIT-4-SMD
MAIN_CAM_POW: MICRO-FIT-4-SMD-PART; MICRO-FIT-4-SMD
MICRO_BOARD: HSEC8-160-01-XX-DV-A
NAV_COM: MICRO-FIT-4-SMD-PART; MICRO-FIT-4-SMD
NAV_POWER: MICRO-FIT-4-SMD-PART; MICRO-FIT-4-SMD
POWER_INPUT: MICRO-FIT-4-SMD-PART; MICRO-FIT-4-SMD
SEC_CAM_1, SEC_CAM_2: MICRO-FIT-4-SMD-PART; MICRO-FIT-4-SMD
SOLENOID_DATA: MICRO-FIT-4-SMD-PART; MICRO-FIT-4-SMD
SOLENOID_POWER: MICRO-FIT-4-SMD-PART; MICRO-FIT-4-SMD
TEMP_SENSOR: MICRO-FIT-4-SMD-PART; MICRO-FIT-4-SMD

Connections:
+3V3: APPLICATION_BOARD.57 (29), APPLICATION_BOARD.58 (29), TEMP_SENSOR.C3
+5V: APPLICATION_BOARD.9 (5), APPLICATION_BOARD.10 (5), APPLICATION_BOARD.11 (6), APPLICATION_BOARD.12 (6), APPLICATION_BOARD.13 (7), APPLICATION_BOARD.14 (7), APPLICATION_BOARD.15 (8), APPLICATION_BOARD.16 (8), APPLICATION_BOARD.17 (9), APPLICATION_BOARD.18 (9), APPLICATION_BOARD.19 (10), APPLICATION_BOARD.20 (10), BUCK_REGULATOR_BOARD.1, BUCK_REGULATOR_BOARD.2 (1), BUCK_REGULATOR_BOARD.3 (2), BUCK_REGULATOR_BOARD.4 (2), BUCK_REGULATOR_BOARD.5 (3), BUCK_REGULATOR_BOARD.6 (3), BUCK_REGULATOR_BOARD.7 (4), BUCK_REGULATOR_BOARD.8 (4), BUCK_REGULATOR_BOARD.9 (5), BUCK_REGULATOR_BOARD.10 (5), BUCK_REGULATOR_BOARD.11 (6), BUCK_REGULATOR_BOARD.12 (6), BUCK_REGULATOR_BOARD.13 (7), BUCK_REGULATOR_BOARD.14 (7), BUCK_REGULATOR_BOARD.15 (8), BUCK_REGULATOR_BOARD.16 (8), BUCK_REGULATOR_BOARD.17 (9), BUCK_REGULATOR_BOARD.18 (9), BUCK_REGULATOR_BOARD.19 (10), BUCK_REGULATOR_BOARD.20 (10), BUCK_REGULATOR_BOARD.21 (11), BUCK_REGULATOR_BOARD.22 (11), BUCK_REGULATOR_BOARD.23 (12), BUCK_REGULATOR_BOARD.24 (12), BUCK_REGULATOR_BOARD.25 (13), BUCK_REGULATOR_BOARD.26 (13), ETH_POWER.C1, ETH_POWER.C2, EXTRA_SERVO.C4, MAIN_CAM_DATA.C1, MAIN_CAM_DATA.C2, MICRO_BOARD.1, MICRO_BOARD.2 (1), MICRO_BOARD.3 (2), MICRO_BOARD.4 (2), MICRO_BOARD.5 (3), MICRO_BOARD.6 (3), MICRO_BOARD.7 (4), MICRO_BOARD.8 (4), MICRO_BOARD.9 (5), MICRO_BOARD.10 (5), MICRO_BOARD.11 (6), MICRO_BOARD.12 (6), NAV_POWER.C1, SOLENOID_DATA.C1
+12V: APPLICATION_BOARD.21 (11), APPLICATION_BOARD.22 (11), APPLICATION_BOARD.23 (12), APPLICATION_BOARD.24 (12), APPLICATION_BOARD.25 (13), APPLICATION_BOARD.26 (13), APPLICATION_BOARD.27 (14), APPLICATION_BOARD.28 (14), APPLICATION_BOARD.29 (15), APPLICATION_BOARD.30 (15), APPLICATION_BOARD.31 (16), APPLICATION_BOARD.32 (16), APPLICATION_BOARD.33 (17), APPLICATION_BOARD.34 (17), BUCK_REGULATOR_BOARD.27 (14), BUCK_REGULATOR_BOARD.28 (14), BUCK_REGULATOR_BOARD.29 (15), BUCK_REGULATOR_BOARD.30 (15), BUCK_REGULATOR_BOARD.31 (16), BUCK_REGULATOR_BOARD.32 (16), BUCK_REGULATOR_BOARD.33 (17), BUCK_REGULATOR_BOARD.34 (17), BUCK_REGULATOR_BOARD.35 (18), BUCK_REGULATOR_BOARD.36 (18), BUCK_REGULATOR_BOARD.37 (19), BUCK_REGULATOR_BOARD.38 (19), BUCK_REGULATOR_BOARD.39 (20), BUCK_REGULATOR_BOARD.40 (20), BUCK_REGULATOR_BOARD.41 (21), BUCK_REGULATOR_BOARD.42 (21), BUCK_REGULATOR_BOARD.43 (22), BUCK_REGULATOR_BOARD.44 (22), BUCK_REGULATOR_BOARD.45 (23), BUCK_REGULATOR_BOARD.46 (23), BUCK_REGULATOR_BOARD.47 (24), BUCK_REGULATOR_BOARD.48 (24), BUCK_REGULATOR_BOARD.49 (25), BUCK_REGULATOR_BOARD.50 (25), MAIN_CAM_POW.C4, NAV_POWER.C4, POWER_INPUT.C1, POWER_INPUT.C2, SEC_CAM_1.C1, SEC_CAM_1.C2, SEC_CAM_2.C1, SEC_CAM_2.C2, SOLENOID_POWER.C1, SOLENOID_POWER.C2
BACK_UP_TEMP_DATA: MICRO_BOARD.49 (25), MICRO_BOARD.50 (25), TEMP_SENSOR.C1
BUCK_SCL: BUCK_REGULATOR_BOARD.53 (27), BUCK_REGULATOR_BOARD.54 (27), MICRO_BOARD.71 (36), MICRO_BOARD.72 (36)
BUCK_SDA: BUCK_REGULATOR_BOARD.51 (26), BUCK_REGULATOR_BOARD.52 (26), MICRO_BOARD.69 (35), MICRO_BOARD.70 (35)
CANH: APPLICATION_BOARD.69 (35), APPLICATION_BOARD.70 (35), BRICKS_COM.C4, MICRO_BOARD.77 (39), MICRO_BOARD.78 (39)
CANL: APPLICATION_BOARD.65 (33), APPLICATION_BOARD.66 (33), BRICKS_COM.C3, MICRO_BOARD.75 (38), MICRO_BOARD.76 (38)
CLK: MICRO_BOARD.63 (32), MICRO_BOARD.64 (32), SOLENOID_DATA.C3
DATA: MICRO_BOARD.65 (33), MICRO_BOARD.66 (33), SOLENOID_DATA.C4
ENABLE: MICRO_BOARD.61 (31), MICRO_BOARD.62 (31), SOLENOID_DATA.C2
GND: APPLICATION_BOARD.37 (19), APPLICATION_BOARD.38 (19), APPLICATION_BOARD.39 (20), APPLICATION_BOARD.40 (20), APPLICATION_BOARD.41 (21), APPLICATION_BOARD.42 (21), APPLICATION_BOARD.43 (22), APPLICATION_BOARD.44 (22), APPLICATION_BOARD.45 (23), APPLICATION_BOARD.46 (23), APPLICATION_BOARD.47 (24), APPLICATION_BOARD.48 (24), APPLICATION_BOARD.49 (25), APPLICATION_BOARD.50 (25), APPLICATION_BOARD.51 (26), APPLICATION_BOARD.52 (26), BUCK_REGULATOR_BOARD.55 (28), BUCK_REGULATOR_BOARD.56 (28), BUCK_REGULATOR_BOARD.57 (29), BUCK_REGULATOR_BOARD.58 (29), BUCK_REGULATOR_BOARD.59 (30), BUCK_REGULATOR_BOARD.60 (30), BUCK_REGULATOR_BOARD.61 (31), BUCK_REGULATOR_BOARD.62 (31), BUCK_REGULATOR_BOARD.63 (32), BUCK_REGULATOR_BOARD.64 (32), BUCK_REGULATOR_BOARD.65 (33), BUCK_REGULATOR_BOARD.66 (33), BUCK_REGULATOR_BOARD.67 (34), BUCK_REGULATOR_BOARD.68 (34), BUCK_REGULATOR_BOARD.69 (35), BUCK_REGULATOR_BOARD.70 (35), BUCK_REGULATOR_BOARD.71 (36), BUCK_REGULATOR_BOARD.72 (36), BUCK_REGULATOR_BOARD.73 (37), BUCK_REGULATOR_BOARD.74 (37), BUCK_REGULATOR_BOARD.75 (38), BUCK_REGULATOR_BOARD.76 (38), BUCK_REGULATOR_BOARD.77 (39), BUCK_REGULATOR_BOARD.78 (39), BUCK_REGULATOR_BOARD.79 (40), BUCK_REGULATOR_BOARD.80 (40), ETH_POWER.C3, ETH_POWER.C4, EXTRA_SERVO.C3, MAIN_CAM_POW.C1, MAIN_CAM_POW.C2, MAIN_CAM_POW.C3, MICRO_BOARD.21 (11), MICRO_BOARD.22 (11), MICRO_BOARD.23 (12), MICRO_BOARD.24 (12), MICRO_BOARD.25 (13), MICRO_BOARD.26 (13), MICRO_BOARD.27 (14), MICRO_BOARD.28 (14), MICRO_BOARD.29 (15), MICRO_BOARD.30 (15), MICRO_BOARD.31 (16), MICRO_BOARD.32 (16), MICRO_BOARD.33 (17), MICRO_BOARD.34 (17), MICRO_BOARD.35 (18), MICRO_BOARD.36 (18), NAV_POWER.C2, NAV_POWER.C3, POWER_INPUT.C3, POWER_INPUT.C4, SEC_CAM_1.C3, SEC_CAM_1.C4, SEC_CAM_2.C3, SEC_CAM_2.C4, SOLENOID_POWER.C3, SOLENOID_POWER.C4, TEMP_SENSOR.C2
LED_PWM: APPLICATION_BOARD.1, APPLICATION_BOARD.2 (1), APPLICATION_BOARD.3 (2), APPLICATION_BOARD.4 (2), APPLICATION_BOARD.5 (3), APPLICATION_BOARD.6 (3), APPLICATION_BOARD.7 (4), APPLICATION_BOARD.8 (4), MAIN_CAM_DATA.C3
MAIN_SERVO: MAIN_CAM_DATA.C4, MICRO_BOARD.73 (37), MICRO_BOARD.74 (37)
NAV_SCL: MICRO_BOARD.83 (42), MICRO_BOARD.84 (42), NAV_COM.C2
NAV_SDA: MICRO_BOARD.81 (41), MICRO_BOARD.82 (41), NAV_COM.C3
SECOND_SERVO: EXTRA_SERVO.C2, MICRO_BOARD.119 (60), MICRO_BOARD.120 (60)
SONAR_DAC: MICRO_BOARD.91 (46), MICRO_BOARD.92 (46), NAV_COM.C1
SONAR_PWM: MICRO_BOARD.67 (34), MICRO_BOARD.68 (34), NAV_COM.C4
TEMP_DATA: APPLICATION_BOARD.59 (30), APPLICATION_BOARD.60 (30), TEMP_SENSOR.C4



Board: 2 copper layers, 122.1 x 122.1 mm, 17 parts (12 on the bottom side), 20 nets.

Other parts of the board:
U$18: ETH_SWITCH

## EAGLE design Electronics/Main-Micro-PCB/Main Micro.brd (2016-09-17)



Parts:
C1: CAP0603-CAP; 0603-CAP
C2, C3: 0.22uF; 0603-CAP
C4, C6, C9, C11, C13, C14, C18: 0.1uF; 0603-CAP
C8: 4.7uF; 0603-CAP
C10, C12: 0.22uF; C0603
C17: 1uF; 0603-CAP
D2, D3, D4, D5: LED0603; LED-0603
D6: DIODE-DO-214AC; DO-214AC
JP1: M07; 1X07
Q1: ASF
R1, R2: 10k; 0603-RES
R3, R4, R9, R10: 4.7K; 0603-RES
R5: 120; 0603-RES
R6: 100K; 0603-RES
R11, R12, R13, R14: 200; 0603-RES
RN2: 2R-NEXBV4V; EXBV4V
SV1, SV2, SV3: FE08-2
T3: FDN340P; SOT-23
T4: AP1117_LIN_REG; SOT223
U$1: STM32F4; LQFP100
U$2, U$3: SWITCH; SW_2512
U$5: MICROUSB; MICRO_B
U$6: MAX3051MAX3051; SOT23-8L
U$8: HSC8PART-60; HSC8-60PINOUUT

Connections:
+3V3: C1.1, C4.1, C6.1, C8.1, C9.1, C10.1, C11.1, C13.1, C14.1, C17.1, C18.1, JP1.6, Q1.4 (VCC), R2.2, R3.2, R4.2, R9.2, R10.2, SV2.16, SV3.8, SV3.10, T4.TAB (VOUT), T4.VOUT, U$1.P6 (VBAT), U$1.P11 (VDD1), U$1.P19 (VDD2), U$1.P21 (VREF+), U$1.P22 (VDDA), U$1.P28 (VDD3), U$1.P50 (VDD4), U$1.P75 (VDD5), U$1.P100 (VDD6), U$3.1, U$6.3 (VCC)
+5V: D6.A, T3.3 (G), U$8.T1, U$8.T2, U$8.T3, U$8.T4, U$8.T5, U$8.T6
ALT_CAMERA_SERVO_MOTOR_PWM: SV1.16, U$1.P96 (PB9), U$8.T60
CANH1: R5.2, U$6.7 (CANH), U$8.T39
CANL1: R5.1, U$6.6 (CANL), U$8.T38
CAN_RX: SV1.12, U$1.P91 (PB5), U$6.4 (RXD)
CAN_TX: SV1.13, U$1.P92 (PB6), U$6.1 (TXD)
CFG: JP1.1
CRS_DV: U$1.P32 (PA7)
GND: C1.2, C2.2, C3.2, C4.2, C6.2, C8.2, C9.2, C10.2, C11.2, C12.2, C13.2, C14.2, C17.2, C18.2, D2.C, D3.C, D4.C, D5.C, JP1.5, Q1.2 (GND), R1.1, R6.1, SV2.15, SV3.1, SV3.7, SV3.9, SV3.11, T4.GND, U$1.P10 (VSS1), U$1.P20 (VSSA), U$1.P27 (VSS2), U$1.P37 (PB2), U$1.P74 (VSS3), U$1.P99 (VSS4), U$2.1, U$5.GND1 (GND), U$5.GND2 (GND), U$5.GND3 (GND), U$5.GND4 (GND), U$5.GND7 (GND), U$5.GND8 (GND), U$5.P4 (ID), U$5.P5 (GND), U$6.2 (GND), U$8.T11, U$8.T12, U$8.T13, U$8.T14, U$8.T15, U$8.T16, U$8.T17, U$8.T18
I2C1_SCL: R9.1, SV1.15, U$1.P95 (PB8), U$8.T42
I2C1_SDA: R10.1, SV1.14, U$1.P93 (PB7), U$8.T41
I2C3_SCL: R3.1, SV2.12, U$1.P67 (PA8), U$8.B36
I2C3_SDA: R4.1, SV2.11, U$1.P66 (PC9), U$8.B35
MAIN_CAMERA_SERVO_MOTOR_PWM: SV1.11, U$1.P90 (PB4), U$8.T37
unnamed: C2.1, U$1.P73 (VCAP_2)
unnamed: C3.1, U$1.P49 (VCAP_1)
unnamed: R1.2, U$1.P94 (BOOT0), U$3.2
unnamed: R2.1, U$1.P14 (NRST), U$2.2
unnamed: R6.2, U$6.8 (RS)
unnamed: RN2.1, U$5.P2 (D-)
unnamed: D3.A, R12.1
unnamed: D5.A, R14.1
unnamed: D4.A, R13.1
unnamed: D2.A, R11.1
unnamed: RN2.2 (1), U$5.P3 (D+)
unnamed: C12.1, D6.C, T3.2 (S), T4.VIN
OSC_IN: Q1.3 (FO), SV3.3, U$1.P12 (PH0)
PA0: U$1.P23 (PA0)
PA3: U$1.P26 (PA3)
PA5: U$1.P30 (PA5)
PA6: U$1.P31 (PA6)
PA10: SV2.14, U$1.P69 (PA10)
PA13: U$1.P72 (PA13)
PA14: U$1.P76 (PA14)
PA15: U$1.P77 (PA15)
PB0: U$1.P35 (PB0)
PB1: U$1.P36 (PB1)
PB14: U$1.P53 (PB14)
PB15: U$1.P54 (PB15)
PC0: U$1.P15 (PC0)
PC2: U$1.P17 (PC2)
PC3: U$1.P18 (PC3)
PC6: SV2.8, U$1.P63 (PC6)
PC7: SV2.9, U$1.P64 (PC7)
PC8: SV2.10, U$1.P65 (PC8)
PC10: SV1.1, U$1.P78 (PC10)
PC12: SV1.3, U$1.P80 (PC12)
PC13: SV3.6, U$1.P7 (PC13)
PC14: SV3.5, U$1.P8 (PC14)
PC15: SV3.4, U$1.P9 (PC15)
PD0: SV1.4, U$1.P81 (PD0)
PD1: SV1.5, U$1.P82 (PD1)
PD2: SV1.6, U$1.P83 (PD2)
PD6: U$1.P87 (PD6)
PD7: U$1.P88 (PD7)
PD8: SV2.1, U$1.P55 (PD8)
PD9: SV2.2, U$1.P56 (PD9)
PD10: U$1.P57 (PD10)
PD11: R11.2, SV2.3, U$1.P58 (PD11)
PD12: R12.2, SV2.4, U$1.P59 (PD12)
PD13: R13.2, SV2.5, U$1.P60 (PD13)
PD14: R14.2, SV2.6, U$1.P61 (PD14)
PD15: SV2.7, U$1.P62 (PD15)
PE0: U$1.P97 (PE0)
PE1: U$1.P98 (PE1)
PE2: SV3.16, U$1.P1 (PE2)
PE3: SV3.15, U$1.P2 (PE3)
PE4: SV3.14, U$1.P3 (PE4)
PE5: SV3.13, U$1.P4 (PE5)
PE6: SV3.12, U$1.P5 (PE6)
PE7: U$1.P38 (PE7)
PE8: U$1.P39 (PE8)
PE9: U$1.P40 (PE9)
PE10: U$1.P41 (PE10)
PE11: U$1.P42 (PE11)
PE12: U$1.P43 (PE12)
PE13: U$1.P44 (PE13)
PE14: U$1.P45 (PE14)
PE15: U$1.P46 (PE15)
PH1: SV3.2, U$1.P13 (PH1)
RST_ETH: JP1.4
RXD0: U$1.P33 (PC4)
RXD1: U$1.P34 (PC5)
SHIFTREG_CLK: SV1.8, U$1.P85 (PD4), U$8.T32
SHIFTREG_DATA: SV1.9, U$1.P86 (PD5), U$8.T33
SHIFTREG_ENABLE: SV1.7, U$1.P84 (PD3), U$8.T31
SONAR_DAC: U$1.P29 (PA4), U$8.B46
SONAR_PWM: SV1.10, U$1.P89 (PB3), U$8.T34
TEMP_BACKUP: SV1.2, U$1.P79 (PC11), U$8.T25
USART3_RX: JP1.3, U$1.P48 (PB11)
USART3_TX: JP1.2, U$1.P47 (PB10)
USBPWR: SV2.13, T3.1 (D), U$1.P68 (PA9), U$5.P1 (VCC)
USB_D+: RN2.3 (2), U$1.P71 (PA12)
USB_D-: RN2.4 (2), U$1.P70 (PA11)
VDD_ETH: JP1.7

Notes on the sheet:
I2C
Micro USB



Board: 2 copper layers, 61.4 x 62.2 mm, 45 parts (15 on the bottom side), 62 nets.

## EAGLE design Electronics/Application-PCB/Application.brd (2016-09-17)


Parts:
C1, C2: 2.2uF; C0603
C3, C4, C5, C6, C9, C11: 0.1uF; C0603
C7: 10nF; C0603
C8: 4.7uF; C0603
C10: 1uF; C0603
C12, C14: 0.22uF; C0603
C_F: 1.0uF; C0603
C_IN1, C_IN2: 2.2uF; C0603
C_OFF: 470pF; C0603
D1: DIODE-DO-214AC; DO-214AC
D2: Yellow; LED-0603
D3: RED; LED-0603
D4: BLUE; LED-0603
D5: GREEN; LED-0603
D6: SL12-E3/61T
L1: 15u; SRN8040
Q1: DMP2012SN-7
Q2: FDN340P; SOT-23
R1, R2: 10K; R0603
R3, R4, R6: 100; R0603
R5: 150; R0603
R7: 4.7K; R0603
R13: 120; R0603
R14: 100K; R0603
RN1: 2R-NEXBV4V; EXBV4V
R_OFF: 7.87K; R0603
R_PD: 10K; R0603
R_SNS: 0.365; R2512
R_UV1: 22.6K; R0603
R_UV2: 13.7K; R0603
S1: BOOT; SW_2512
S2: RESET; SW_2512
SV1: Left; FE08-2
SV2: Top; FE08-2
SV3: Bottom; FE08-2
SV4: Right; FE08-2
U1: LM3409HV; VSSOP-10
U2: MAX3051; SOT23-8L
U3: U3; SOT223
U4: STM32F405; LQFP64
U5: MICROUSB; MICRO_B
U$2: HSCPART; HSC8-40PINOUUT
Y1: 8.000MHZ; ASF

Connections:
+3V3: C3.1, C4.1, C5.1, C6.1, C7.1, C8.1, C9.1, C10.1, C14.1, R2.2, R7.2, S1.2, SV1.1, SV1.14, SV2.15, SV3.3, SV3.15, SV4.15, U2.3 (VCC), U3.TAB (VOUT), U3.VOUT, U4.1 (VBAT), U4.13 (VDDA), U4.19 (VDD), U4.32 (VDD), U4.48 (VDD), U4.64 (VDD), U$2.B29, Y1.4 (VCC)
+5V: D1.A, Q2.3 (G), U$2.B5, U$2.B6, U$2.B7, U$2.B8, U$2.B9, U$2.B10
+12V: C_F.1, C_IN1.1, C_IN2.1, R_SNS.2, R_UV2.2, U1.8 (CSP), U1.10 (VIN), U$2.T11, U$2.T12, U$2.T13, U$2.T14, U$2.T15, U$2.T16, U$2.T17
BOOT0: R1.2, S1.1, SV2.11, U4.60 (BOOT0)
CAM_LEDV: L1.2, R_OFF.1, U$2.T1, U$2.T2, U$2.T3, U$2.T4
CAM_LED_PWM: R_PD.1, SV3.6, U4.22 (PA6)
CAN2_RX: SV4.1, U2.4 (RXD), U4.33 (PB12)
CAN2_TX: SV4.2, U2.1 (TXD), U4.34 (PB13)
CANH: R13.1, U2.7 (CANH), U$2.B35
CANL: R13.2, U2.6 (CANL), U$2.B33
DBUG_LED1: R3.2, SV4.8, U4.40 (PC9)
DBUG_LED2: R4.2, SV4.7, U4.39 (PC8)
DBUG_LED3: R5.2, SV4.6, U4.38 (PC7)
DBUG_LED4: R6.2, SV4.5, U4.37 (PC6)
GND: C1.2, C2.2, C3.2, C4.2, C5.2, C6.2, C7.2, C8.2, C9.2, C10.2, C11.2, C12.2, C14.2, C_IN1.2, C_IN2.2, C_OFF.2, D2.C, D3.C, D4.C, D5.C, D6.2 (A), R1.1, R14.2, R_UV1.1, S2.2, SV1.11, SV2.16, SV3.2, SV3.11, U1.5 (GND), U1.DAP, U2.2 (GND), U3.GND, U4.12 (VSSA), U4.18 (VSS), U4.28 (PB2), U4.63 (VSS), U5.GND1 (GND), U5.GND2 (GND), U5.GND3 (GND), U5.GND4 (GND), U5.GND7 (GND), U5.GND8 (GND), U5.P4 (ID), U5.P5 (GND), U$2.T19, U$2.T20, U$2.T21, U$2.T22, U$2.T23, U$2.T24, U$2.T25, U$2.T26, Y1.2 (GND)
L1: D6.1 (C), L1.1, Q1.1 (D)
unnamed: RN1.1, U5.P2 (D-)
unnamed: R_UV1.2, R_UV2.1, U1.1 (UVLO)
unnamed: C_OFF.1, R_OFF.2, U1.4 (COFF)
unnamed: C_F.2, U1.9 (VCC)
unnamed: Q1.3 (S), R_SNS.1, U1.7 (CSN)
unnamed: R_PD.2, U1.3 (EN)
unnamed: Q1.2 (G), U1.6 (PGATE)
unnamed: RN1.2 (1), U5.P3 (D+)
unnamed: Q2.1 (D), U5.P1 (VCC)
unnamed: C12.1, D1.C, Q2.2 (S), U3.VIN
unnamed: D2.A, R3.1
unnamed: D3.A, R4.1
unnamed: D4.A, R5.1
unnamed: D5.A, R6.1
unnamed: R14.1, U2.8 (RS)
NRST: C11.1, R2.1, S2.1, SV1.7, U4.7 (NRST)
OSCIN: SV1.5, U4.5 (PH0_OSCIN), Y1.3 (FO)
OSCOUT: SV1.6, U4.6 (PH1_OSCOUT)
PIN2: SV1.2, U4.2 (PC13)
PIN3: SV1.3, U4.3 (PC14)
PIN4: SV1.4, U4.4 (PC15)
PIN8: SV1.8, U4.8 (PC0)
PIN9: SV1.10, U4.9 (PC1)
PIN10: SV1.9, U4.10 (PC2)
PIN11: SV1.12, U4.11 (PC3)
PIN14: SV1.13, U4.14 (PA0_WKUP)
PIN15: SV1.16, U4.15 (PA1)
PIN16: SV1.15, U4.16 (PA2)
PIN17: SV3.1, U4.17 (PA3)
PIN20: SV3.4, U4.20 (PA4)
PIN21: SV3.5, U4.21 (PA5)
PIN23: SV3.7, U4.23 (PA7)
PIN24: SV3.8, U4.24 (PC4)
PIN25: SV3.10, U4.25 (PC5)
PIN26: SV3.9, U4.26 (PB0)
PIN27: SV3.12, U4.27 (PB1)
PIN29: SV3.14, U4.29 (PB10)
PIN30: SV3.13, U4.30 (PB11)
PIN35: SV4.3, U4.35 (PB14)
PIN36: SV4.4, U4.36 (PB15)
PIN41: SV4.10, U4.41 (PA8)
PIN42: SV4.9, U4.42 (PA9)
PIN43: SV4.12, U4.43 (PA10)
PIN46: SV4.13, U4.46 (PA13)
PIN49: SV2.1, U4.49 (PA14)
PIN50: SV2.2, U4.50 (PA15)
PIN51: SV2.3, U4.51 (PC10)
PIN52: SV2.4, U4.52 (PC11)
PIN53: SV2.5, U4.53 (PC12)
PIN54: SV2.6, U4.54 (PD2)
PIN55: SV2.7, U4.55 (PB3)
PIN56: SV2.8, U4.56 (PB4)
PIN57: SV2.10, U4.57 (PB5)
PIN59: SV2.12, U4.59 (PB7)
PIN61: SV2.14, U4.61 (PB8)
PIN62: SV2.13, U4.62 (PB9)
TEMP_SENS: R7.1, SV2.9, U4.58 (PB6), U$2.B30
USBD+: RN1.3 (2), SV4.14, U4.45 (PA12)
USBD-: RN1.4 (2), SV4.11, U4.44 (PA11)
VCAP_1: C1.1, SV3.16, U4.31 (VCAP_1)
VCAP_2: C2.1, SV4.16, U4.47 (VCAP_2)

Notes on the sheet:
: pins 19, 32, 48, 64
: pins 18, 63
Between VDDA and VSSA
One for each VDD
Conect to any one VDD
Micro USB
Yes we CAN!
Random LEDs



Board: 2 copper layers, 52.8 x 68.6 mm, 54 parts (12 on the bottom side), 77 nets.

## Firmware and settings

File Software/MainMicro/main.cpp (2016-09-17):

#include "main.h"

#include "print.h"
#include "packet_in.h"
#include "packet_out.h"
#include "matrices.h"
#include "imu.h"
#include "pressure.h"
#include "servo.h"
#include "pi_controller.h"


/*
 * CAN2 GPIO Configuration
 * PB5  ------> CAN2_RX
 * PB6  ------> CAN2_TX 
 * CAN_HandleTypeDef hcan2
 *
 */

/*
 * I2C1 GPIO Configuration
 * PB7  ------> I2C1_SDA
 * PB8  ------> I2C1_SCL 
 * I2C_HandleTypeDef hi2c1;
 *
 */


/*
 * TIM5 GPIO Configuration
 * PA0  ------> TIM5_CH1
 * Main Camera servo
 * TIM_OC_InitTypeDef sConfigOC;
 * TIM_HandleTypeDef htim5
 * TIM_CHANNEL_1
 *
 * PA3  ------> TIM5_CH4
 * Alternate camera servo
 * TIM_OC_InitTypeDef sConfigOC;
 * TIM_HandleTypeDef htim5
 * TIM_CHANNEL_4
 *
 */

/*
 * USART1 GPIO Configuration
 * PB10  ------> USART3_TX
 * PB11  ------> USART3_RX
 * UART_HandleTypeDef huart3;
 *
 */


/*
 * USEFULL FUNCTIONS
 *
 * RED; BLUE; GREEN; YELLOW
 * void LedOn(int ledNum);
 * void LedOff(int ledNum);
 * void LedToggle(int ledNum);
 *
 */


/*
 * Example how to send can code
 *
 * Sets the size of the packet. Max 8
 * CanHandle.pTxMsg->DLC = 8; 
 *
 * Set up the data
 * CanHandle.pTxMsg->Data[0] = 5;
 * CanHandle.pTxMsg->Data[1] = 246;
 * CanHandle.pTxMsg->Data[2] = 17;
 *
 * Send the message over can
 * HAL_CAN_Transmit(&hcan2, 10);
 *
 */


/* Variables used in the motor controlling code */
PIController piController; //stabalization controller structure
vect6 force_output;	//vector containing desired logitudinal rotational force for the ROV
int16_t * force_input;
float pressure_mbar;
PacketIn *packet;
PacketOut *packetOut;

bool RECEIVED_NEW_DATA = 0;

int main(void) {
	// Initializes all of the pins!
	initEverything();

	packet = new PacketIn();
	packetOut = new PacketOut();
	
	HAL_UART_Receive_DMA(&huart3, packet->getArray(), PACKET_IN_LENGTH);


	packetOut->setThrusterStatus(1);
	packetOut->setPressure(1.0);
	packetOut->setTemp(36.0);
	packetOut->setIMU_Lx(1.0);	// Linear x
	packetOut->setIMU_Ly(1.0);	// Linear y
	packetOut->setIMU_Lz(1.0);	// Linear z
	packetOut->setIMU_Rx(1.0);	// Rotational x
	packetOut->setIMU_Ry(1.0);	// Rotational y
	packetOut->setIMU_Rz(1.0);	// Rotational z


	// IMU init
	IMU imu = IMU(&hi2c1);

	// Pressure init	
	Pressure pressure = Pressure(ADDRESS_HIGH, &hi2c1);
	pressure.reset();
	pressure.begin();

	// PIController inits
	PIController piController = PIController();
	piController.start();
	piController.setNewRotation(vect3Make(0,0,0));
	piController.setNewP(0.001);
	piController.setNewI(0.001);

	// Can Packet Size Init
	hcan2.pTxMsg->DLC = 8;

	// Camera Servo Init
	servo cameraServo = servo(&htim3, &sConfigOC, TIM_CHANNEL_1);
	cameraServo.setStart(0.725);
	cameraServo.setRange(1.39);

	while (1) {

		if (RECEIVED_NEW_DATA) {

			// IMU Sensor:
			/* Commented out until I2C isn't locking up
			imu.get_linear_accel(); // Gets linear movement
			imu.retrieve_euler(); // Gets angular movement
			*/

			// Pressure Sensor:
			/* Commented out until I2C isn't locking up
			pressure_mbar = pressure.getPressure(ADC_4096); // Returns mbar pressure from sensor.

			// Pressure Debug Test:
			if (pressure_mbar > 500 && pressure_mbar < 1500) {
				LedToggle(RED);
			}
			*/
			
			
			// PID Controller:
			/* Commented out until IMU working
			// Update piController's sensor data and compute its PID modulated output to the Rotational force vector.
			piController.sensorInput(vect3Make((int16_t) (imu.rX() * 1000), (int16_t) (imu.rY() * 1000), (int16_t) (imu.rZ() * 1000)),
			vect3Make((int16_t) (imu.aX() * 1000), (int16_t) (imu.aY() * 1000), (int16_t) (imu.aZ() * 1000)), HAL_GetTick());
			force_output.R = piController.getOutput();
			*/


			// Update PacketOut Data:
			packetOut->setThrusterStatus(1);
			packetOut->setTemp(36);

			/*
			packetOut->setPressure(pressure_mbar);
			packetOut->setIMU_Lx(imu.lX());	// Linear x 	
			packetOut->setIMU_Ly(imu.lY());	// Linear y 	
			packetOut->setIMU_Lz(imu.lZ());	// Linear z 	
			packetOut->setIMU_Rx(imu.rX());	// Rotational x 
			packetOut->setIMU_Ry(imu.rY());	// Rotational y 
			packetOut->setIMU_Rz(imu.rZ());	// Rotational z 
			*/


			/*
			// Commented out until full server testing is working
			cameraServo.set((packet->getCameraServo() <= 128 ? 90 - (packet->getCameraServo() * (180 / 256)) : (packet->getCameraServo() * (180 / 256))));
			*/



			int16_t* thrusters = packet->getThrusters();

			// Sets the info for the logitudinal forces
			hcan2.pTxMsg->Data[0] =	'L';
			memcpy(&hcan2.pTxMsg->Data[1], &thrusters[0], 6);
			hcan2.pTxMsg->Data[7] = packet->getHydraulicsPump();
			
			// Send the longitudinal forces
			if (HAL_CAN_Transmit(&hcan2, 100) == HAL_OK) {
				LedOn(BLUE);
			} else {
				LedOff(BLUE);
			}

			// Sets the info for the rotational forces
			hcan2.pTxMsg->Data[0] =	'R';
			memcpy(&hcan2.pTxMsg->Data[1], &thrusters[3], 6);
			hcan2.pTxMsg->Data[7] = packet->getPIDControl(); //The PID Control byte

			// Send the rotational forces
			if (HAL_CAN_Transmit(&hcan2, 100) == HAL_OK) {
				LedOn(BLUE);
			} else {
				LedOff(BLUE);
			}


		    // Send packet data back up
		    packetOut->send();

			RECEIVED_NEW_DATA = false;
		}

		LedToggle(ORANGE);


		//Delay Loop 10ms
		HAL_Delay(10);
	}
}


/* This is where messages from CAN are received */
void HAL_CAN_RxCpltCallback(CAN_HandleTypeDef* CanHandle){

	//example on how to use this in callback function
	if ((CanHandle->pRxMsg)->StdId == POW_CAN_ID && (CanHandle->pRxMsg)->IDE == CAN_ID_STD){

		if ((CanHandle->pRxMsg)->DLC == 8) {
			
		}

		bool motor_status = 0xFF;

		for (int i = 0; i < (CanHandle->pRxMsg)->DLC; i++) {
			motor_status = motor_status && ((CanHandle->pRxMsg)->Data[i] == MOTOR_OK);
		}

	}

	// Restarts the interrupt
	HAL_CAN_Receive_IT(CanHandle, CAN_FIFO0);
}

//this is run when the a serial message is sent
void HAL_UART_TxCpltCallback(UART_HandleTypeDef *UartHandle){

}

//this is run when a serial message is received
void HAL_UART_RxCpltCallback(UART_HandleTypeDef *UartHandle){

	//set the Serial to read more data again
	HAL_UART_Receive_DMA(&huart3, (uint8_t *)packet->getArray(), PACKET_IN_LENGTH);


	packet->recieve();

	//force_input = packet->getThrusters();
	//force_output = vect6Make(force_input[0], force_input[1], force_input[2], force_input[3], force_input[4], force_input[5]);
	//piController.setNewRotation(force_output.R);


	//Indicate that we have new data, so send out can messages and other things
	RECEIVED_NEW_DATA = true;


	LedToggle(GREEN);
}

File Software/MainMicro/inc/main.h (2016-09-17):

#ifndef __MAIN_H
#define __MAIN_H

#include "stm32f4xx_hal.h"
#include "stm32f4xx_it.h"
#include "stm32f4xx.h"
#include "print.h"
#include <stdint.h>
#include <string.h>
#include "init.h"
#include <stm32f407xx.h>

#define POW_CAN_ID  0x11
#define APP_CAN_ID  0x12
#define CAN_ID      0x13

#define BLUE   0
#define GREEN  1
#define RED    2
#define ORANGE 3

#define MAX(x,y) ((x > y) ? (x) : (y))
#define MIN(x,y) ((x > y) ? (y) : (x))

#define Main_Camera_Servo_PWM_Pin       GPIO_PIN_4
#define Main_Camera_Servo_PWM_GPIO_Port GPIOB
#define Alt_Camera_Servo_PWM_Pin        GPIO_PIN_3
#define Alt_Camera_Servo_PWM_GPIO_Port  GPIOA
#define Sonar_DAC_Pin                   GPIO_PIN_4
#define Sonar_DAC_GPIO_Port             GPIOA
#define Sonar_Pwm_Pin                   GPIO_PIN_5
#define Sonar_Pwm_GPIO_Port             GPIOA

#define MOTOR_OK 0xAB


#endif /* __MAIN_H */

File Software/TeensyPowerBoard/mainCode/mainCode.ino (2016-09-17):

#include <i2c_t3.h>
#include "matrices.h"
#include "overseer_teensy.h"
//#include "thrust_mapper.h"
#include <FlexCAN.h>
#include <kinetis_flexcan.h>
#include <stdlib.h>
#include <Servo.h>
//#include "hydraulics.h"
#include "thrusterPWMWrapper.h"
#include "Adafruit_PWMServoDriver.h"

#define MAIN_CAN_ID 0x13
#define TIMEOUT_LIMIT 500 

Adafruit_PWMServoDriver driver = Adafruit_PWMServoDriver();

thrusterPWMWrapper motor0(1,0); 
thrusterPWMWrapper motor1(2,0);
thrusterPWMWrapper motor2(3,0);
thrusterPWMWrapper motor3(4,0); 
thrusterPWMWrapper motor4(5,0); 
thrusterPWMWrapper motor5(6,0);
thrusterPWMWrapper motor6(7,0);
thrusterPWMWrapper motor7(8,0);

thrusterPWMWrapper unmodified_motors[8] = {motor0, motor1, motor2, motor3, motor4, motor5, motor6, motor7};
thrusterPWMWrapper motors[8] = {motor0, motor1, motor2, motor3, motor4, motor5, motor6, motor7};

int led = 13;
int d = 200;
FlexCAN can(500000);
OverseerT overseer;
//Hydraulics hydraulics = Hydraulics();
uint8_t * hydraulicsTarget;
CAN_message_t message;
int16_t thrusters[6];
volatile uint_fast8_t RampTicker;
long period = 0;
long timeout = 0;
int16_t thrusterRemapping[3];

void setup() {
  //setup the PWM driver

  driver.begin();
  driver.setPWMFreq(1600);

  
  // put your setup code here, to run once:

  pinMode(led, OUTPUT);

  //filter.id = 0x11;
  //message.timeout = 100;
  
  
  Serial.begin(115200);
  Serial.print("hi there");

  /*message.len = 8;
  message.id = 0x13;
  for( int idx=0; idx<8; ++idx ) {
    message.buf[idx] = 0x00;
  }*/
  //start i2c
  Serial.println("STARTING\n");
  Wire.begin(I2C_MASTER, 0x00, I2C_PINS_18_19, I2C_PULLUP_INT, I2C_RATE_400);
  Wire.setDefaultTimeout(3000);
  Serial.println("WIRE STARTED\n");
//  overseer.update(vect6Make(0,0,0,0,0,0), vect3Make(0,0,0), 0); 
  Serial.print("Hi");

  can.begin();

  overseer = OverseerT();
  *hydraulicsTarget = 0;

  pinMode(13, OUTPUT);
  digitalWrite(13, HIGH);

  
}

void loop() {
  delay(1);
  Serial.print("Main loop");
  // put your main code here, to run repeatedly:

  //Serial.printf("%d\t%d\t%d\t%d\t%d\t%d\n",thrusters[0],thrusters[1],thrusters[2],thrusters[3],thrusters[4],thrusters[5]);
  
  //digitalWrite(led, LOW);
  


  //overseer.checkForUpdate();

  // If Timeout is exceeded, STOP MOTORS:
  if (timeout >= TIMEOUT_LIMIT)
  {
    //int8_t enabled = 0;
    //overseer.update(vect6Make(thrusters[0],thrusters[1],thrusters[2],thrusters[3],thrusters[4],thrusters[5]), vect3Make(0,0,0), enabled);
    overseer.sendToMotors(vect8Make(0,0,0,0,0,0,0,0));
    timeout++;
  }
  else
    overseer.sendToMotors(vect8Make(thrusters[0], thrusters[1], thrusters[2], thrusters[3], thrusters[4], thrusters[5], thrusters[6], thrusters[7]));
  /*else if (RampTicker >= 20)
  {
    overseer.doRamping();
    RampTicker = 0;
	  //hydraulics.set(hydraulicsTarget);
  }else{
    timeout++;
    RampTicker++;
  }*/
 
  //period = millis();
  if (can.available()) {
  if(can.read(message)) {
    digitalWrite(led, HIGH);
    
    //if message came from main micro
    if (message.id == MAIN_CAN_ID && message.len == 8) {
      switch (message.buf[0]) {
        case 'L': // longitudinal data
          memcpy(&thrusters[0], &(message.buf[1]), 1);
          memcpy(&thrusters[1], &(message.buf[2]), 1);
          memcpy(&thrusters[2], &(message.buf[3]), 1);
          memcpy(&thrusters[3], &(message.buf[4]), 1);
          memcpy(&thrusters[4], &(message.buf[5]), 1);
          memcpy(&thrusters[5], &(message.buf[6]), 1);
          break;
        case 'R': // rotational data
        {
          memcpy(&thrusters[6], &(message.buf[1]), 1);
          memcpy(&thrusters[7], &(message.buf[2]), 1);
          memcpy(hydraulicsTarget, &(message.buf[3]), 1);
    
          //char enabled = 255; //249 to remove motors 6 and 7 -- change to 246 to remove 5 and 8 instead
          Serial.println(" CAN: ");
          //overseer.update(vect6Make(thrusters[0],thrusters[1],thrusters[2],thrusters[3],thrusters[4],thrusters[5]), vect3Make(0,0,0), enabled);
          timeout = 0;
          
          //Serial.print("\n");
        }
          break;
        
        case 'T': //remap the motors 
        {
          memcpy(&thrusterRemapping[0],&(message.buf[1]), 2);
          memcpy(&thrusterRemapping[1],&(message.buf[2]), 2);
          memcpy(&thrusterRemapping[2],&(message.buf[3]), 2);

          int i = 0;
          int val = 0;
          for(i = 0; i < 8; i++)
          {
             val = 4 * (thrusterRemapping[2] && 1 << i) + 2 * (thrusterRemapping[1] && 1 << i) + (thrusterRemapping[0] && 1 << i);
             motors[i] = unmodified_motors[val];
          }
         }
             
          break;
          
      }
    }
  }
  //digitalWrite(led, LOW);
  Serial.println(" ");
  }
}

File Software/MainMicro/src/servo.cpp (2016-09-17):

/* Put all of your #includes and #defines up here   */

/*
 *   int prescaller  = 1000000;
 *   int period = 3333;
 *   int pulse = 500;
 *
 *   //this is how we set how fast ticks happen (pwm is measured in clock ticks not seconds) and we set the length of the period of the alternating pulse width
 *	 TimHandle.Init.Prescaler         = uhPrescalerValue;
 *	 TimHandle.Init.Period            = period;
 *
 */



#include "servo.h"


servo::servo(TIM_HandleTypeDef* HTIM, TIM_OC_InitTypeDef* SCONFIG, uint32_t CHANNEL)
{
    timerHandler = HTIM;
    sConfig = SCONFIG;
    channel = CHANNEL;

    startPosition = 0.75;
    range = 1.5;

}

//sets the angle of the servo from 0 to 180 degrees
void servo::set(uint8_t angle)
{
    if(angle > 180)
       angle = 180;

    sConfig->Pulse = ((double) timerHandler->Init.Period / 3.33) * range * angle / 180 + ((double) timerHandler->Init.Period / 3.33) * startPosition;

    HAL_TIM_PWM_ConfigChannel(timerHandler, sConfig, channel);
    HAL_TIM_PWM_Start(timerHandler, channel);
}

//sets the starting pulse length that will corespond to an angle of 0 in miliseconds
void servo::setStart(double start)
{
    startPosition = start;
}

//sets the range that the pulse length will vary in mili seconds
void servo::setRange(double Range)
{
    range = Range;
}

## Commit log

2016-09-17 Add all the things
    [12-5Convertor.brd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]
2016-09-17 Changed names
    [12-5Convertor.brd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]
2016-09-27 Updated Application board
    [Application map.brd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]
2016-09-27 updated power conversion and main micro
    [12-5Convertor.brd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]
2016-09-27 Got rid of a bunch of things that never should have been in Github
    [Navboard.brd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]
2016-09-27 adjusted naming conventions to technical report
    [Navboard.brd, Navboard.sch, Power-Conversion.brd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]
2016-10-04 added initial mechanical stuff
    [#6 EYEBOLT.SLDPRT, 010000_rear_head.sldprt, 012_95-D.sldasm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]
2016-10-04 added parts library
    [#1.4-20 - 91831A029.SLDPRT, #1.4-20 .SLDPRT, #10 - 0.19 - 0.0625 - 99872A300.SLDPRT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]
2016-10-29 Removed unneeded mechanical files
    [A. Frame Epsilon.x_t, A. Power Distribution Box Welded.SLDASM, Ball Bearing.SLDPRT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]
2016-12-10 temp probe
2016-12-10 Added readmes and removed camera boxes
    [Alternate Camera Box Cap.SLDPRT, Alternate Camera Box.SLDPRT, Camera Box Assembly.SLDASM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]
2016-12-27 Added more mechanical readmes
    [Baseplate.SLDPRT, Claw of moving part.SLDPRT, Claw of stationary part.SLDPRT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]

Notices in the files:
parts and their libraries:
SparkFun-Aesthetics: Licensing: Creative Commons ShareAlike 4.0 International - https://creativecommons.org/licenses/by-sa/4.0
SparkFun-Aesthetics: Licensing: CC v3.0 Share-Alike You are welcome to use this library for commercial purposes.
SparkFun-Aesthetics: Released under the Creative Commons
